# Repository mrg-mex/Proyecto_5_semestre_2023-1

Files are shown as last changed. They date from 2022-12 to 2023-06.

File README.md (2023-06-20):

# Proyecto_5_semestre_2023-1
# Diseño y simulación de un robot manipulador móvil

# Robótica serial adaptable

# Participantes
- Erik Peña Medina (responsable)
- Garcia Oñate Miguel Angel
- Mendoza Reyes Carlos Mauricio
- Lazcano Romero Eduardo Alejandro
- Torres Guerrero Adair

# Objetivo
Diseñar e generar los elmentos para la simulación y construcción de un manipulador móvil, compuesto por una base móvil omnidireccional y un robot serial Dofbot.

# Metas
- Determinar los parámetros relacionados con las dimensines de los elementos que componene al robot.
- Establecer una distribución de los elementos que conforman la base móvil de tal manera que sus dimensiones sean considetnes las dimensiones del robot ROSMASTER X3 PLUS ROS Robot.
- Realizar el diseño a detalle del robot en CAD y generar los elementos de la simulación virtual del robot.
- Diseño y construcción de los circuitos de la PCB necesarios para la implimientación del robot. 

---
# Productos
- Diseño a detalle del la plataforma móvil.
- Desarrollo de los elementos de una simulación Virtual del robot en formato URDF.
- Diseño y realización de los circuitos de control y de potencia del robot en formato PCB.
- Desarrollo de los elementos para la construcción del manipulador móvil de manera física.

---
## Primer día, mié 30/11/22
- Instalacion SW 2020
- Inicio de planeación → probablemente iniciaremos con esquemáticos del robot
ROSMASTER X3 PLUS para comparar sus dimensiones y distribución con el actual
(Requerimos SW)
- Descargamos dofbot-cad-min.zip, el cad del robot. En este repo GITHUB
---
## Segundo dia, lun 05/12/22
- afecta la forma de la base? por que mantener el track?
- qué lleva el piso inferior? el comercial es mas chico, por qué lo queremos mas
grande?
- donde posicionar los soportes del motor?

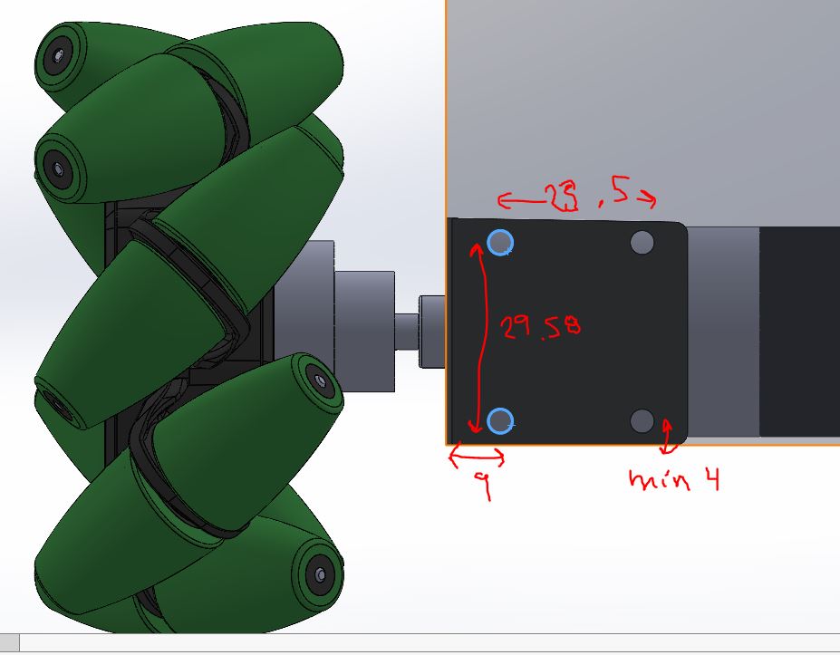
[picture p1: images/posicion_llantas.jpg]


---
## Lun 12/12/2022 fue puente
---
## Tercer dia, mie 14/12/22
- cads de partes faltantes
- distribucion de los elementos en los pisos
- tamaño de los pisos y alturas chance

Abajo se muestran las dimensiones preliminares del tamaño de los pisos

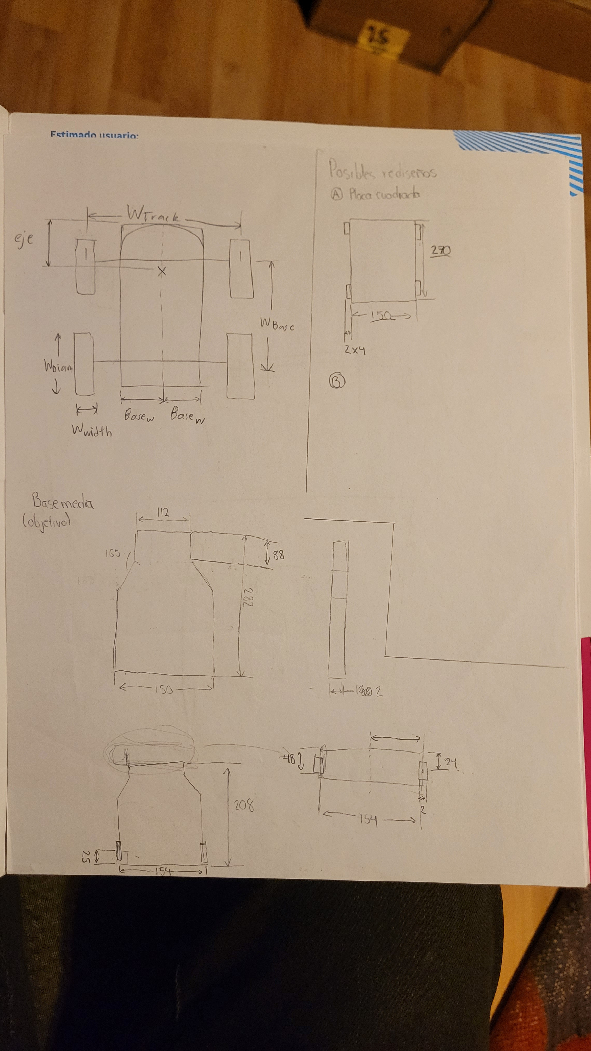
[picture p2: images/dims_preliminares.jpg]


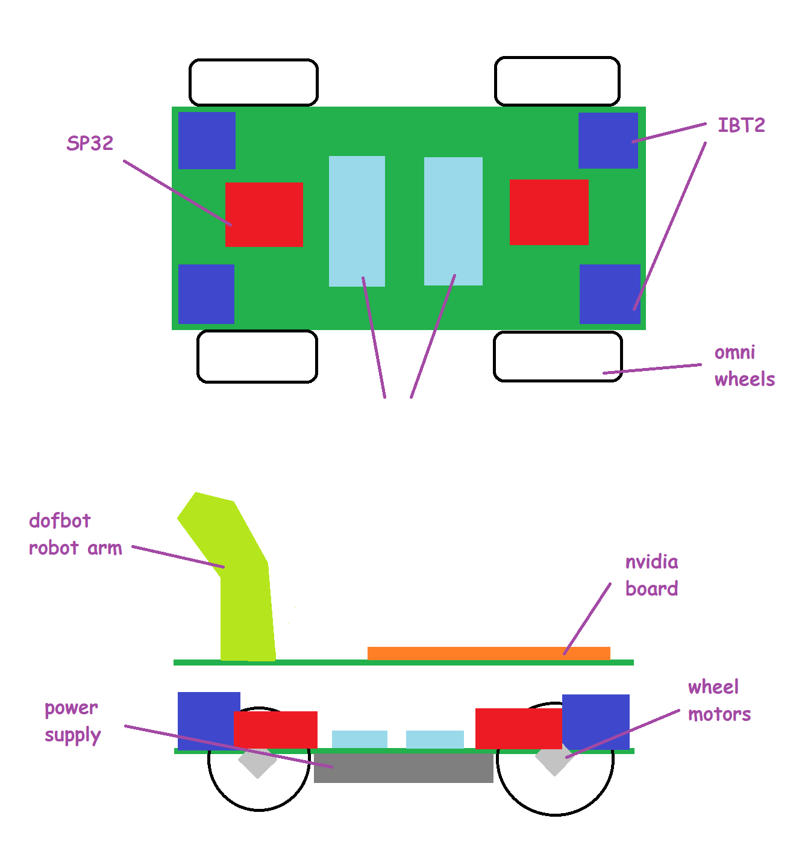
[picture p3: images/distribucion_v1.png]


---

## Cuarto día, mie 11/01/23
- La placa inferior del diseño comercial tiene unas dimensiones de 280 mm x 150 mm. Sin embargo, estas medidas no pueden ser tomadas debido al tamaño de la batería que chocaría con los motores.
Se propuso una placa inferior de 200 mm x 320 mm basándonos en las medidas del primer prototipo fabricado con MDF por el profesor Erik Peña Medina. La placa seguía siendo pequeña para posicionar la batería en la parte inferior.
Al final se propuso una placa de 320 mm x 170 mm la cual permitió tener el suficiente espacio para distribuir los componentes y realizar los respectivos agujeros para el cableado.

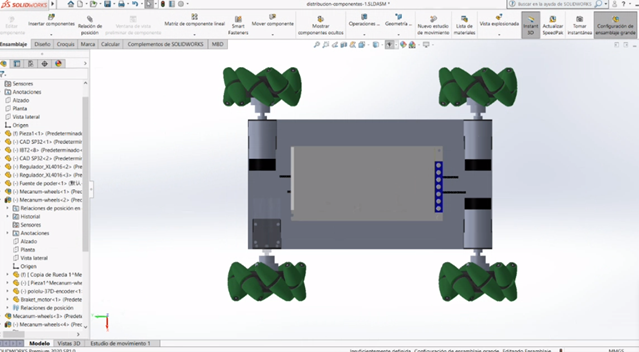
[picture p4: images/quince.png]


### Distancia entre motores
Para la propuesta de la distancia entre motores el equipo se basó en la distancia del robot comercial la cual es de 44 mm. Esta distancia entre motores es importante ya que le dará estabilidad al robot móvil.

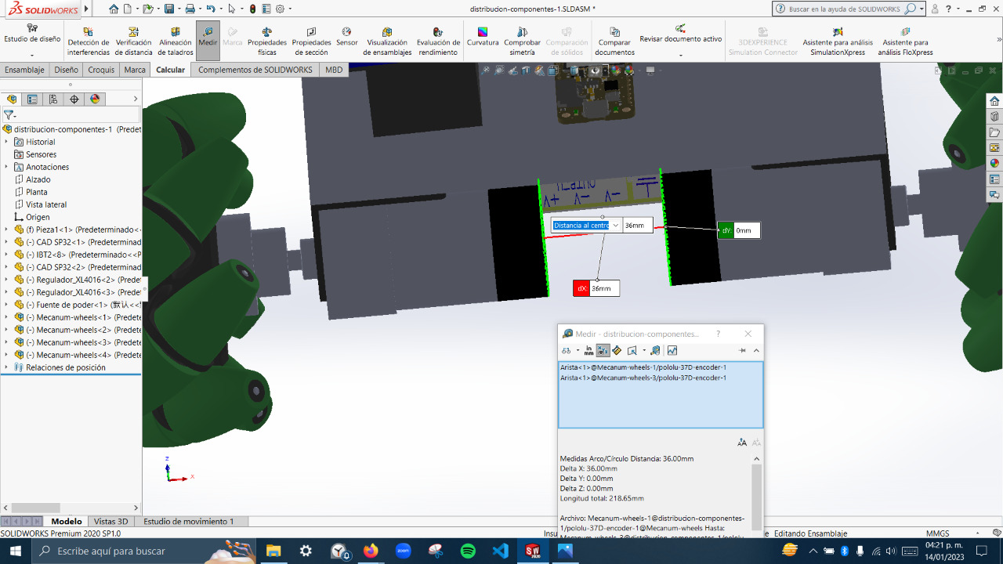
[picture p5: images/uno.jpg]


### Orientación de IBT2
Por cada motor existirá un IBT2 y la para proponer la orientación más óptima de estos componentes se consideró las conexiones entre componentes.

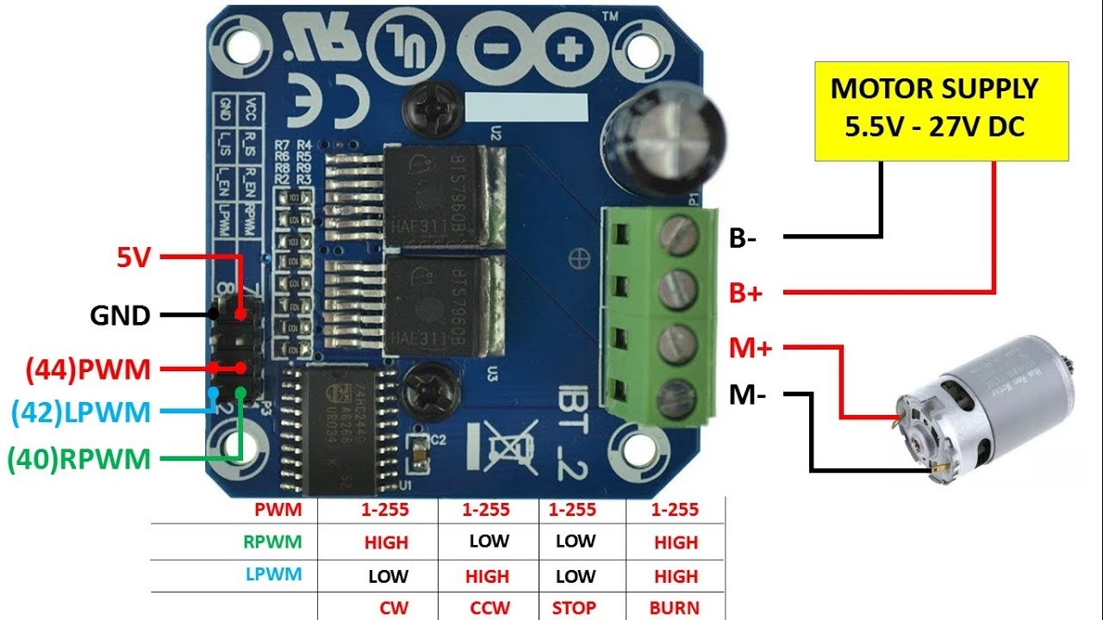
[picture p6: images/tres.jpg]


A continuación, se muestra el diagrama de conexiones entre componentes:

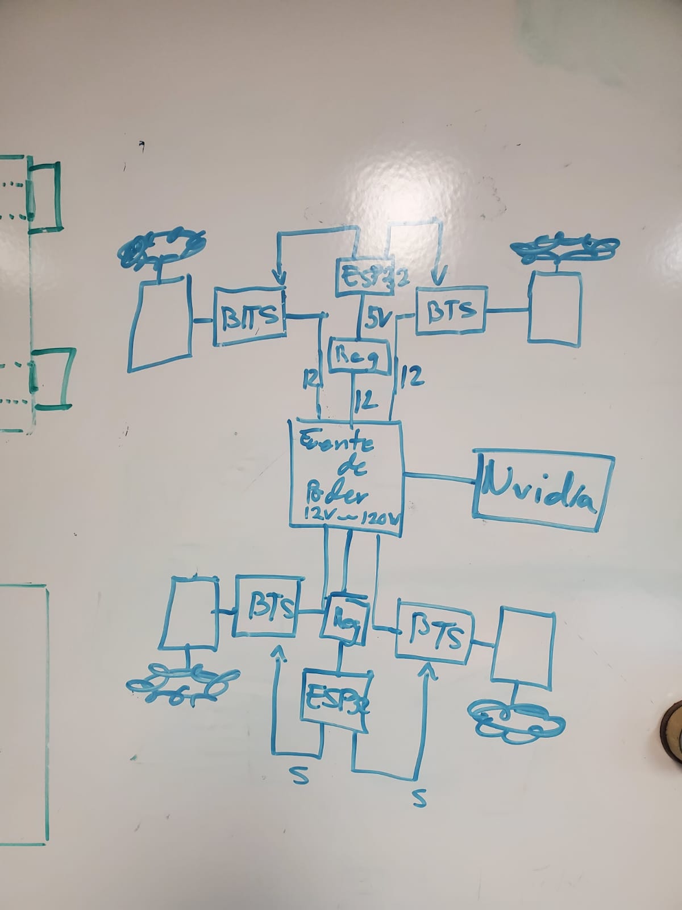
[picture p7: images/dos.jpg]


### Orientación final propuesta:

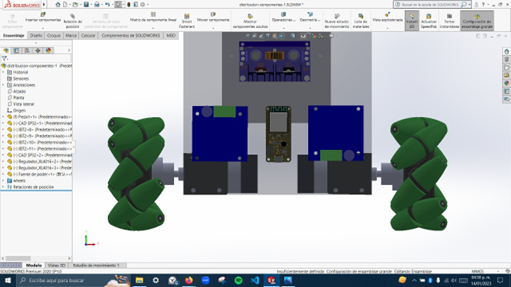
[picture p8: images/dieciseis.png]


### Propuesta montaje de PCB
Al no conocer las dimensiones de la PCB se propuso crear un piso intermedio en voladizo. Se muestra la propuesta en la siguiente imagen:
 
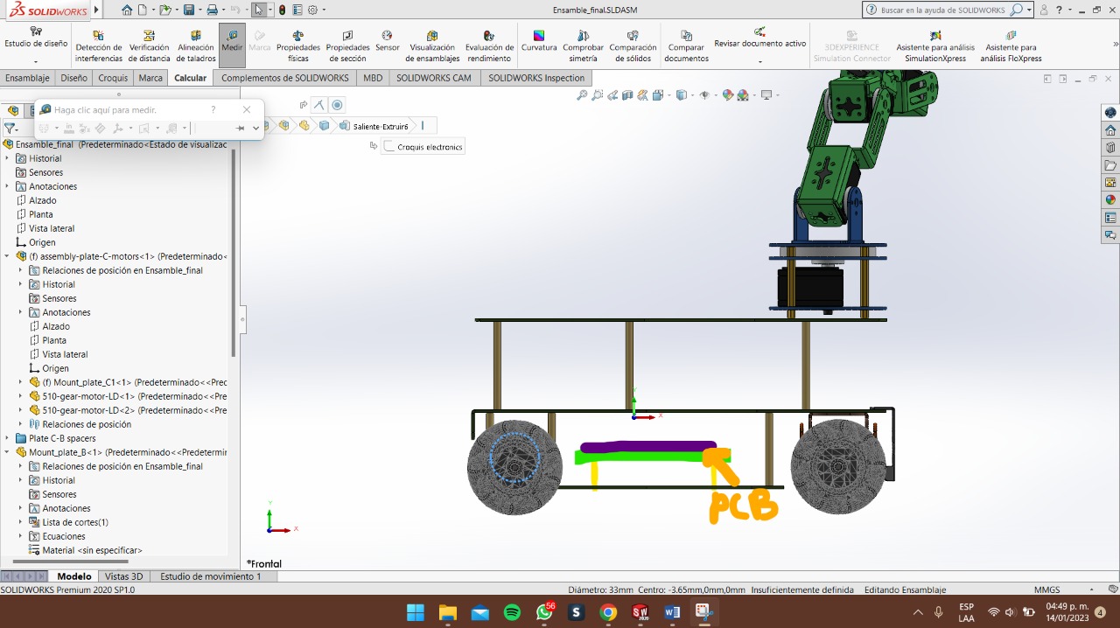
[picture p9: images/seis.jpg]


Para simular la PCB y realizar el montaje de los componentes se insertaron dos protoboards.

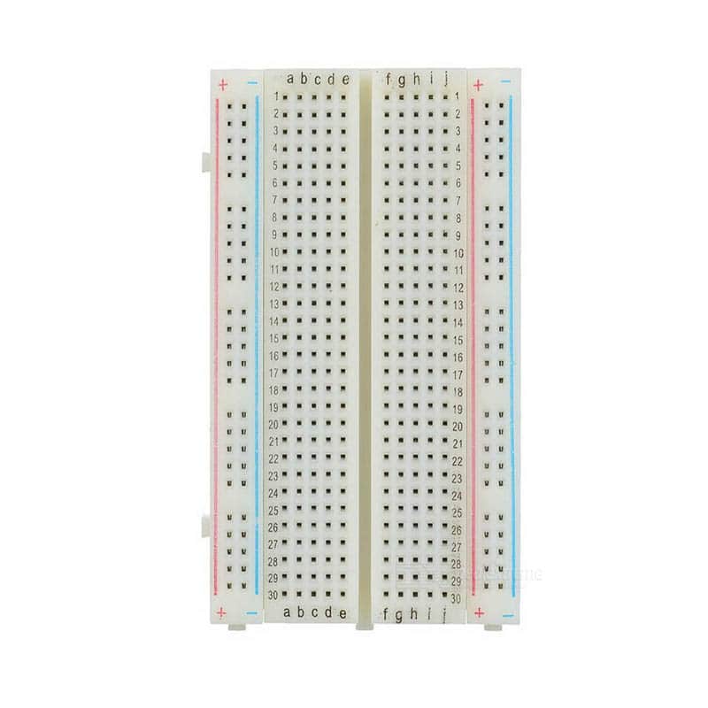
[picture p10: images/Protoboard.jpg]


### Ensamble de componentes principales
Nos encontramos con el problema de no poder ensamblar los componentes a la placa inferior debido a todo el espacio que ocupa la batería. Para solucionar esto, se propuso un piso superior en donde se montaron cada uno de los IBT2. 

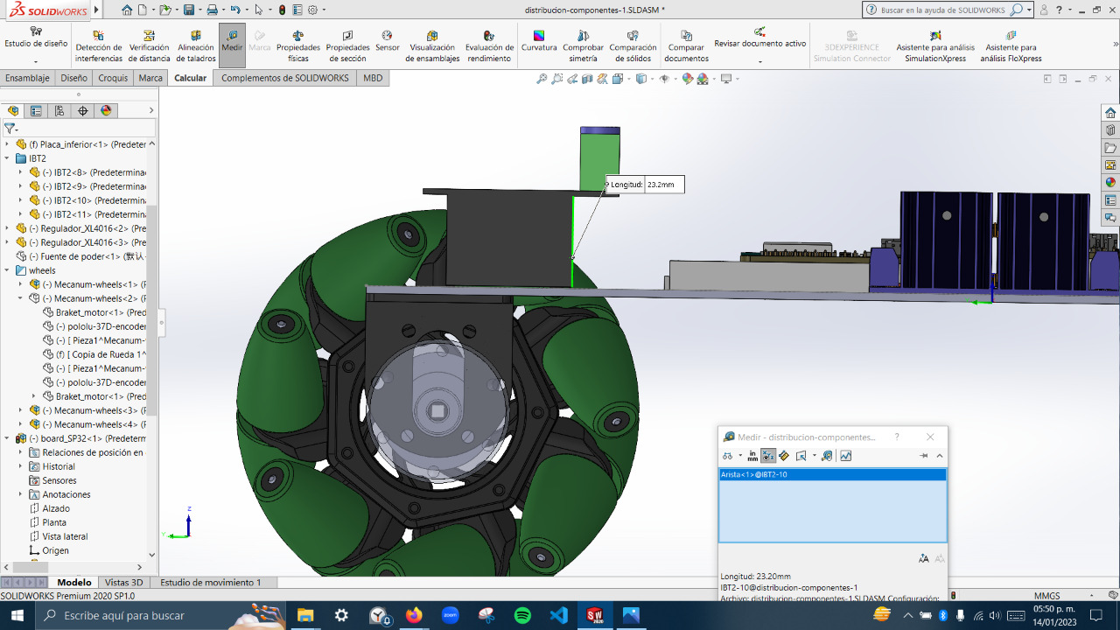
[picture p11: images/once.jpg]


Los IBT2 se montaron en voladizo esto ayudará a mejorar el paso del aire a través de los disipadores.

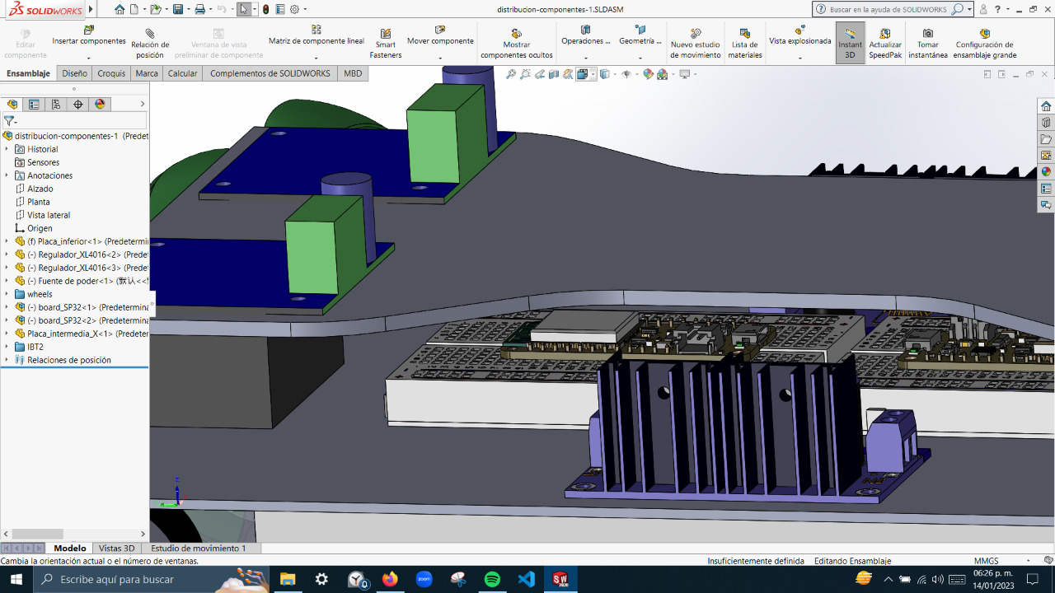
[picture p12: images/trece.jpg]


### Diseño del segundo Piso del Robot, para ensamblaje del brazo.
En este punto, se contempló que nuestro diseño (una vez optimizado el espacio) debería contener unas columnas que nos permitieran dejar un piso libre
para ensamblar el brazo del modelo comercial.

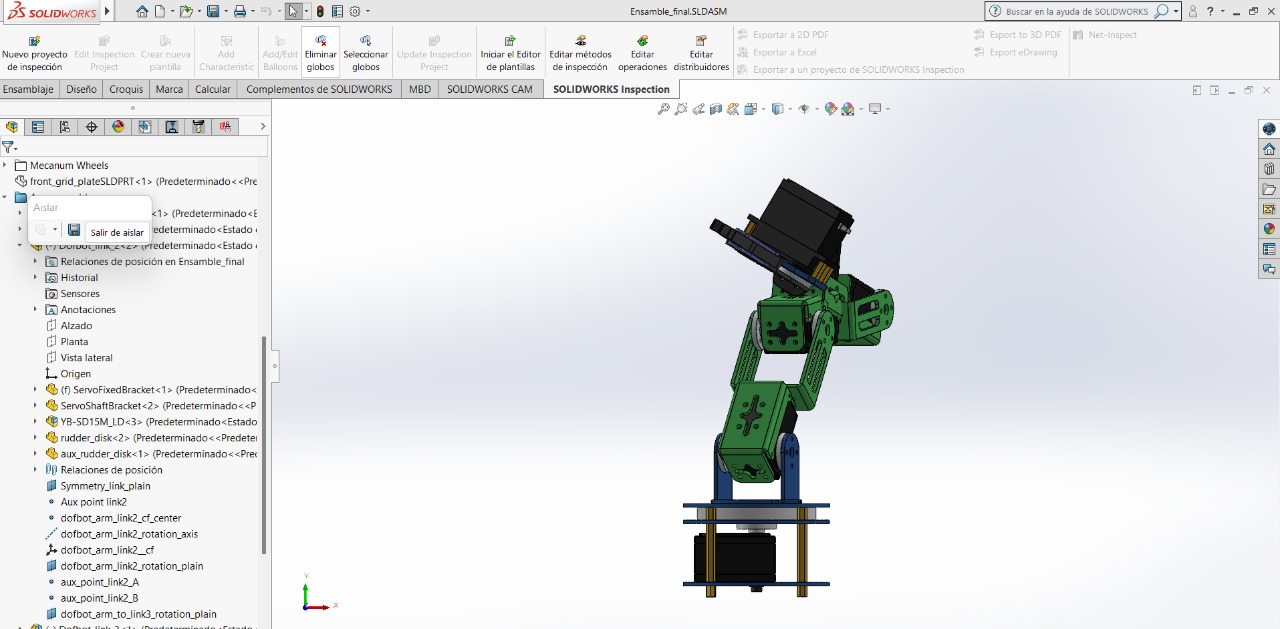
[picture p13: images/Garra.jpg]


### Implementación del segundo piso del robot
Una vez planificado el espacio donde se implementarán las columnas, se procedió a realizar el modelado final:
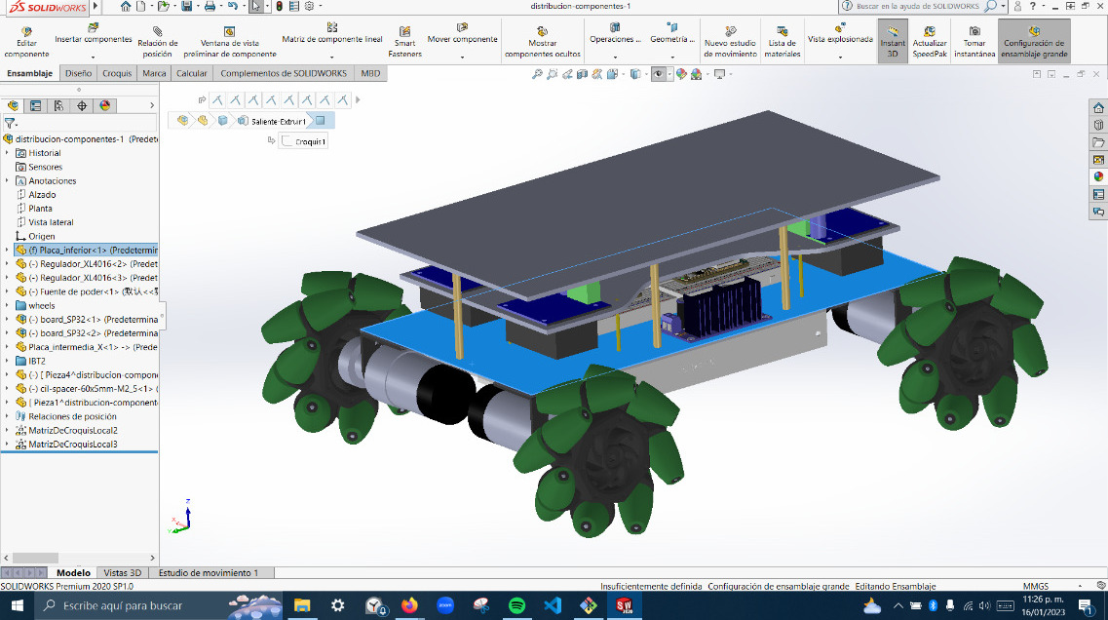
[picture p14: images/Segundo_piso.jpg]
Imagen de una segunda plataforma sobre el diseño previamente mostrado


### Ensamble del brazo robotico:
Para esta parte, se buscó establecer la pieza cercano al centro de masa, de tal modo que no afectara la localización de la Nvidia y pudiera cubrir los requerimientos 
planteados por el profesor.

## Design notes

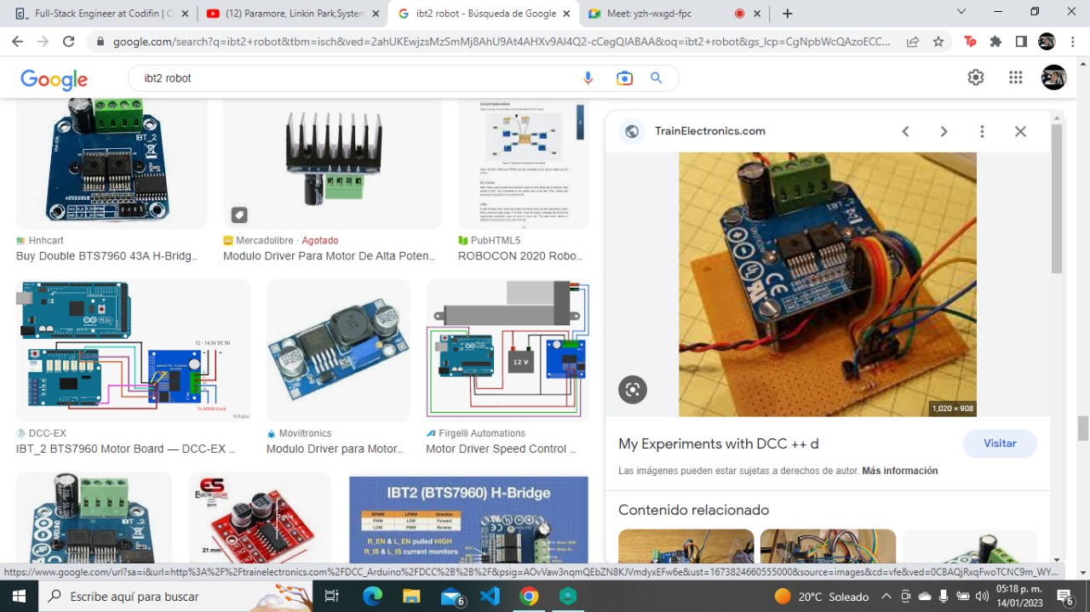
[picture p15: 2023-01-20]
images/siete.jpg

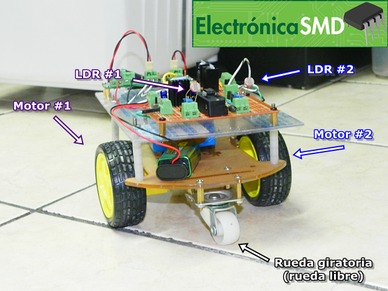
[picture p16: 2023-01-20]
images/cinco.jpg

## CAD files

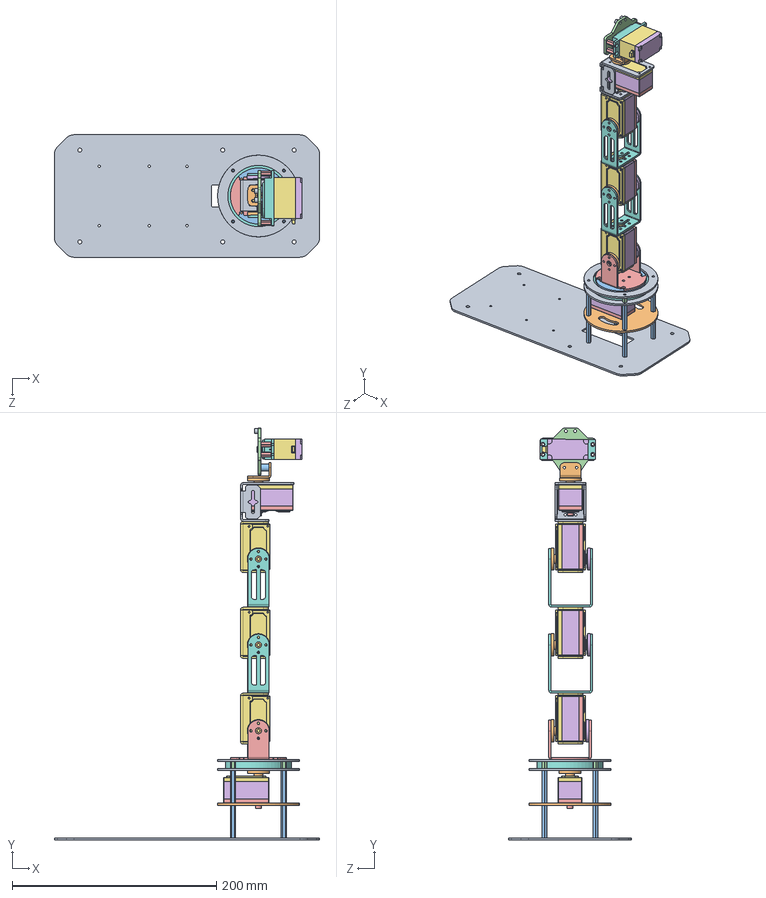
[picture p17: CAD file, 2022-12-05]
Arm_urdf.SLDASM
260.0 x 403.5 x 120.0 mm
Placa_Base
base_ring_2
M2,5_hex_standoff_32mm x 8
Hex_nut_7mm_ig_ig_3.6mm x 4
YB-SD15M-Bottom-Cover-LD x 5
YB-SD15M-Middle-Cover-LD x 5
YB-SD15M-Top-Cover-LD x 5
Sealed-Ball-Bearing-50x65x7mm
Base_ring x 2
rudder_disk x 5
Base_spin_disk x 2
cil_7mm_spacer x 4
link_shaft_bracket
aux_rudder_disk x 3
ServoFixedBracket x 3
ServoShaftBracket x 2
ServoFixedBracket_Type_C
shaft-rudder-coupler
Cil-spacer-7x10-inn-3mm x 2
Mount-plate
Hex_nut_10mm_ig_ig_2,5mm x 4
YB-SSERVO-6KG-Bottom
YB-SSERVO-6KG-Middle
YB-SSERVO-6KG-Top
Cil-spacer-3x5-inn-3mm x 2

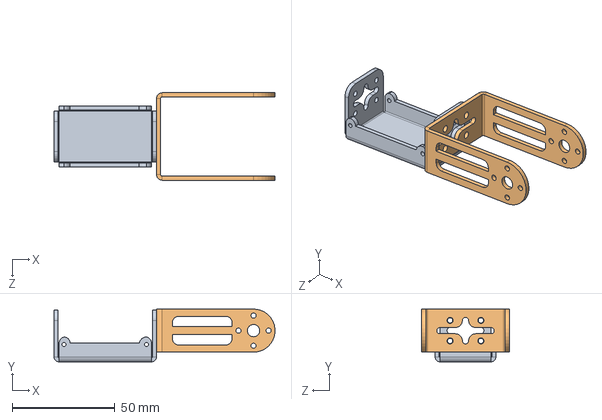
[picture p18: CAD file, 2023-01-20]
Ensable_final_robotica/Ensamble_robot_comercial/Link_type_A.SLDASM
107.7 x 25.7 x 42.7 mm
ServoFixedBracket
ServoShaftBracket

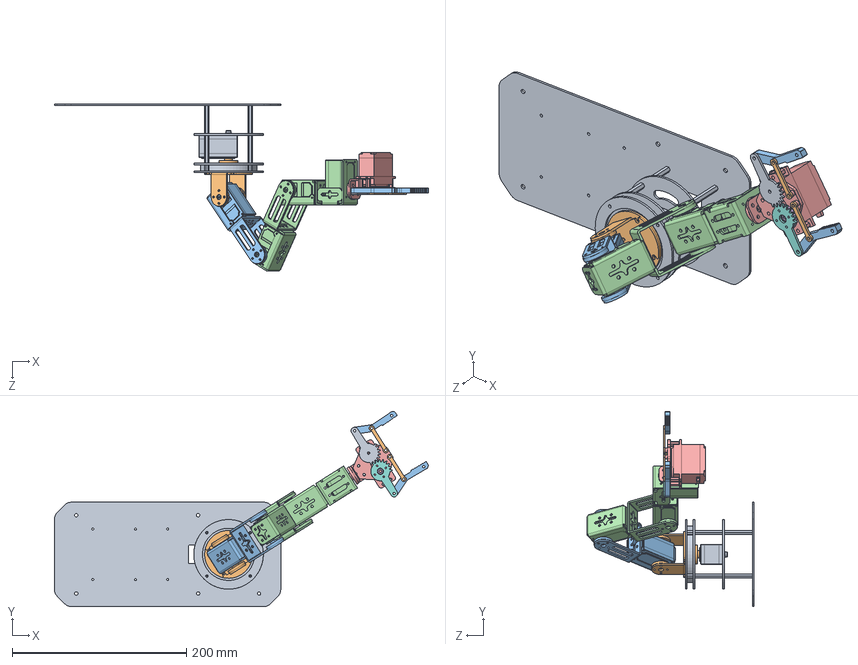
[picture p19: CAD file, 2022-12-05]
Simplificado/Dofbot_esamble_simplify.SLDASM
429.7 x 224.2 x 192.1 mm
Dofbot_base_link_simplificado
Dofbot_link_1_sim
Dofbot_link_2_sim
Dofbot_link4_simplificado
Dofbot_link_5_simplificado
rudder_disk
finger-spacer
finger-rgt-gear
finger-lft-gear
finger-bar x 2
rfinger_tip x 2
Dofbot_link_3_sim

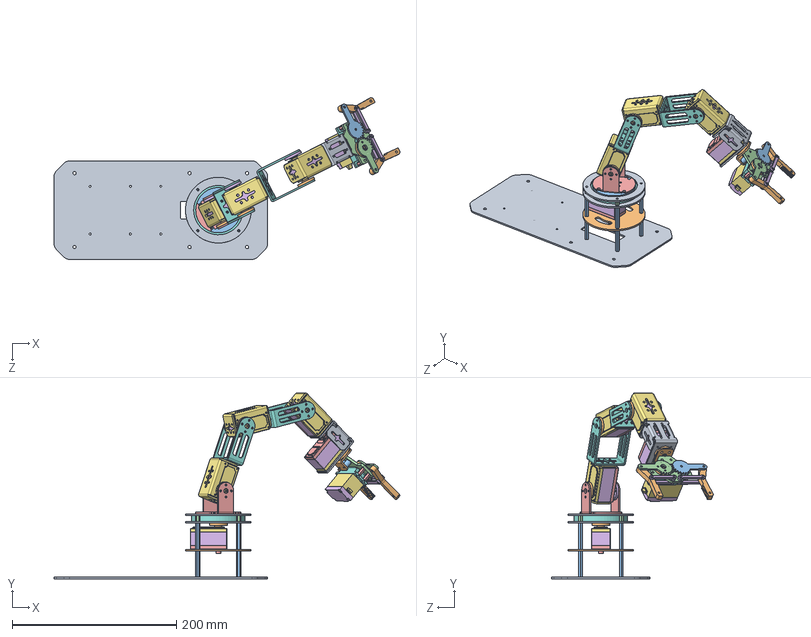
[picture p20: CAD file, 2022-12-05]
Arm_Simscape.SLDASM
421.1 x 226.0 x 197.0 mm
Placa_Base
base_ring_2
M2,5_hex_standoff_32mm x 8
Hex_nut_7mm_ig_ig_3.6mm x 4
YB-SD15M-Bottom-Cover-LD x 5
YB-SD15M-Middle-Cover-LD x 5
YB-SD15M-Top-Cover-LD x 5
Sealed-Ball-Bearing-50x65x7mm
Base_ring x 2
rudder_disk x 6
Base_spin_disk x 2
cil_7mm_spacer x 4
link_shaft_bracket
aux_rudder_disk x 3
ServoFixedBracket x 3
ServoShaftBracket x 2
ServoFixedBracket_Type_C
shaft-rudder-coupler
Cil-spacer-7x10-inn-3mm x 2
Mount-plate
Hex_nut_10mm_ig_ig_2,5mm x 4
YB-SSERVO-6KG-Bottom
YB-SSERVO-6KG-Middle
YB-SSERVO-6KG-Top
Cil-spacer-3x5-inn-3mm x 4
rfinger_tip x 2
finger-lft-gear
finger-rgt-gear
finger-spacer
finger-bar x 4

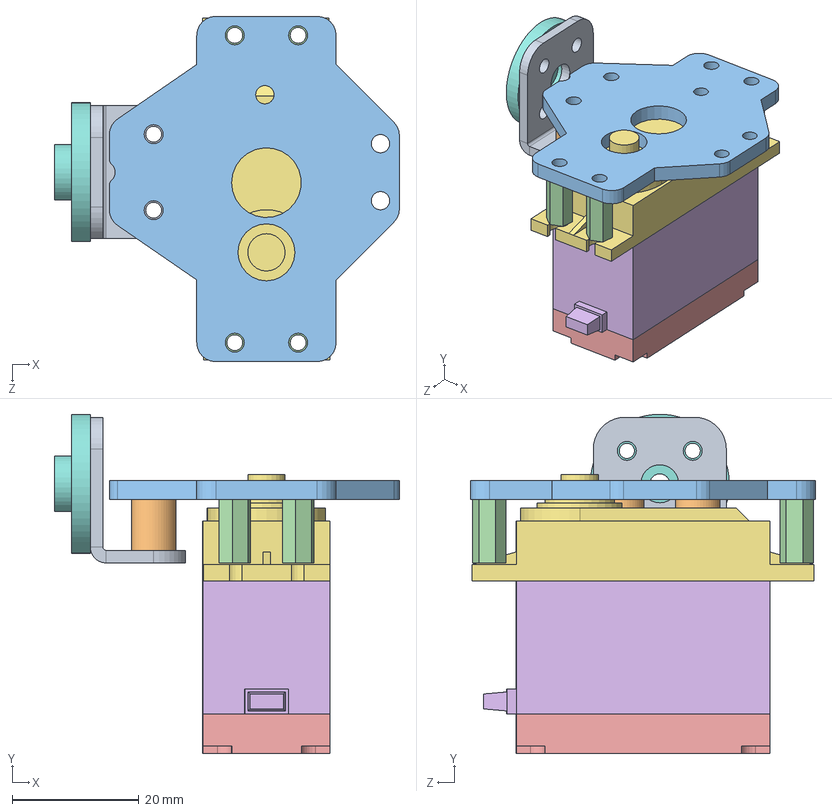
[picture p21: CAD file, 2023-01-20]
Ensable_final_robotica/Ensamble_robot_comercial/Dofbot_link_5.SLDASM
54.5 x 53.6 x 54.5 mm
shaft-rudder-coupler
Cil-spacer-7x10-inn-3mm x 2
Mount-plate
Hex_nut_10mm_ig_ig_2,5mm x 4
YB-SSERVO-6KG-Bottom
YB-SSERVO-6KG-Middle
YB-SSERVO-6KG-Top
rudder_disk

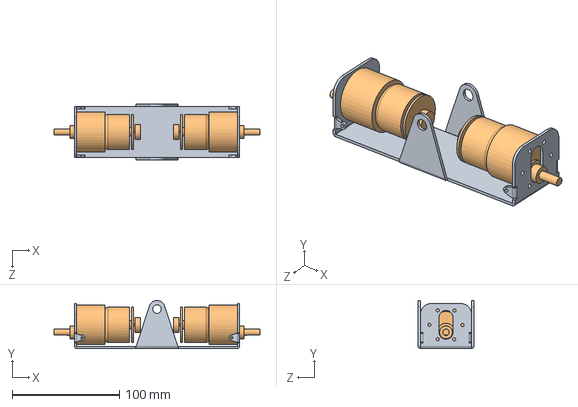
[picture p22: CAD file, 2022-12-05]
Ensable_final_robotica/Ensamble_robot_comercial/Movil/assembly-plate-Cb-motors.SLDASM
192.2 x 44.8 x 52.0 mm
Mount_plate_C2_bottom
510-gear-motor-LD x 2

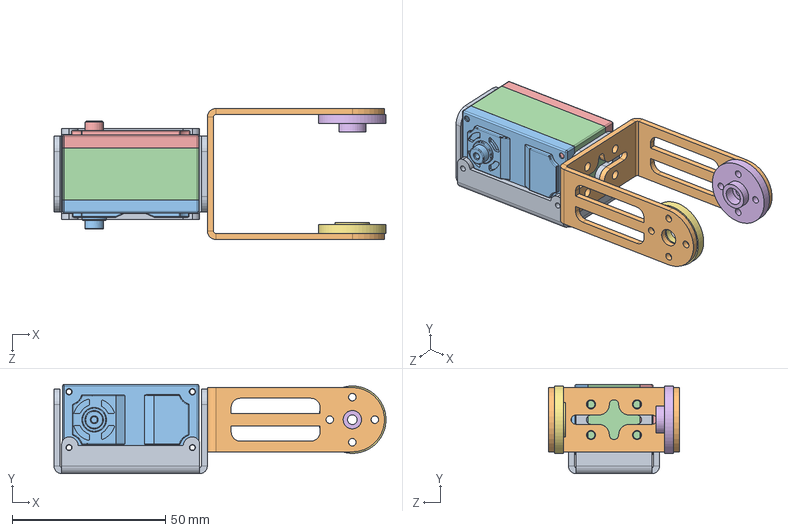
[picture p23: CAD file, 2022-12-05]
Simplificado/Dofbot_link_2_simplificado.SLDASM
108.2 x 29.1 x 42.7 mm
ServoFixedBracket
ServoShaftBracket
YB-SD15M-Bottom-Cover-LD
YB-SD15M-Middle-Cover-LD
YB-SD15M-Top-Cover-LD
rudder_disk
aux_rudder_disk

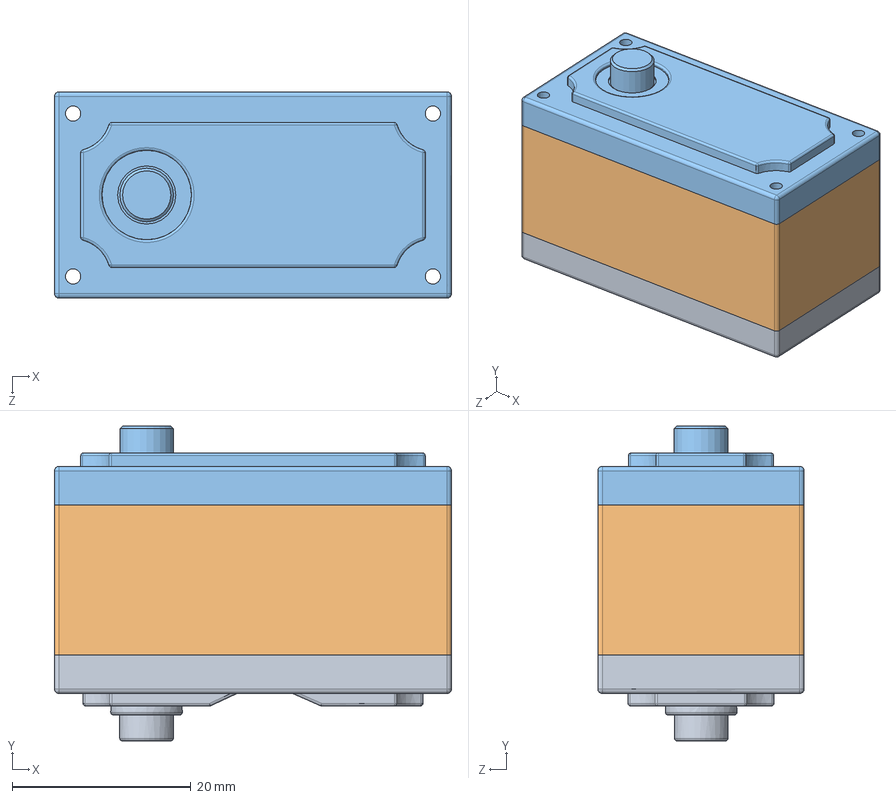
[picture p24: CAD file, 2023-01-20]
Ensable_final_robotica/Ensamble_robot_comercial/YB-SD15M-LD/YB-SD15M_LD.SLDASM
44.4 x 35.2 x 23.1 mm
YB-SD15M-Bottom-Cover-LD
YB-SD15M-Middle-Cover-LD
YB-SD15M-Top-Cover-LD

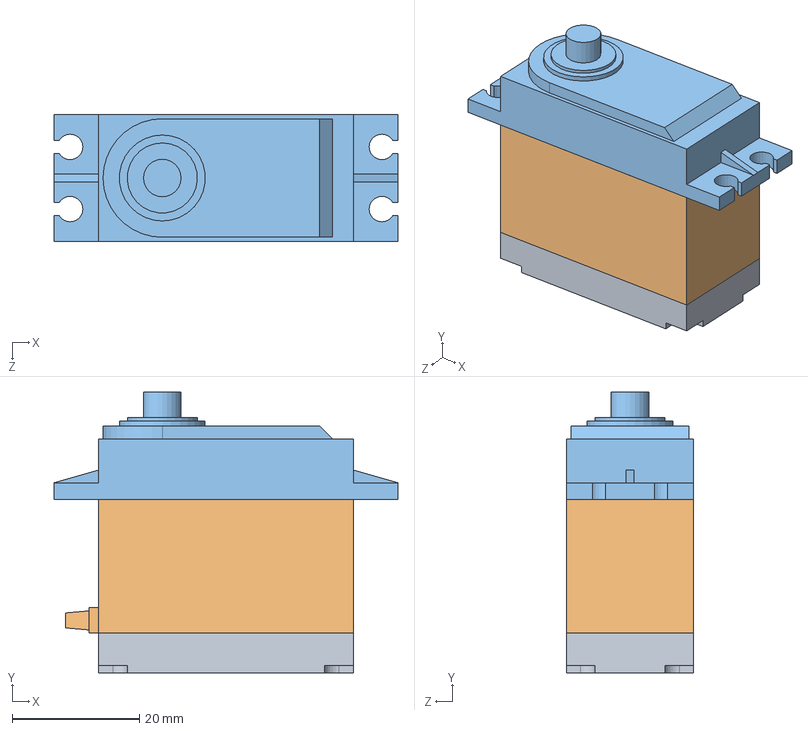
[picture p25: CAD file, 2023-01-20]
Ensable_final_robotica/Ensamble_robot_comercial/YB-SERVO-6KG-LD/YB-SERVO-6KG-LD.SLDASM
54.0 x 44.1 x 20.0 mm
YB-SSERVO-6KG-Bottom
YB-SSERVO-6KG-Middle
YB-SSERVO-6KG-Top

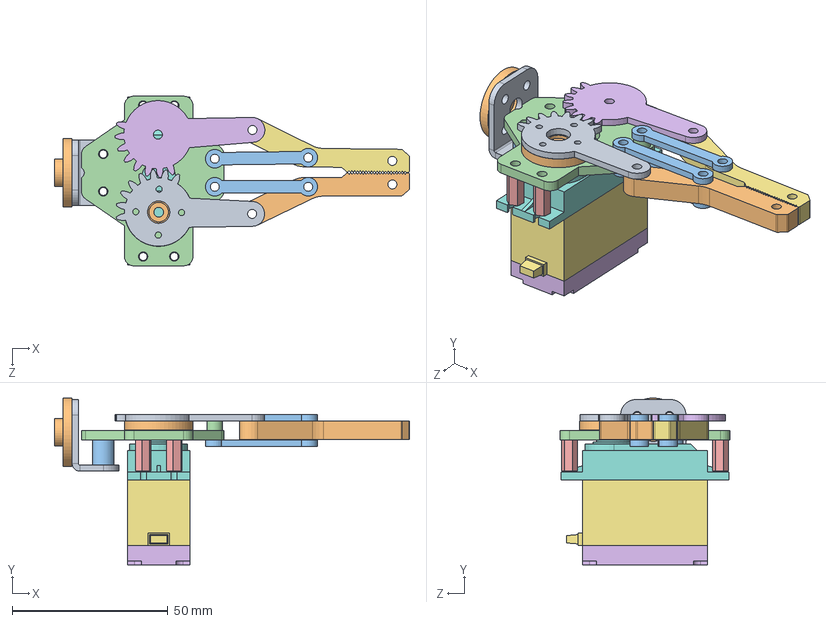
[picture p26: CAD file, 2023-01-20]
Ensable_final_robotica/Ensamble_robot_comercial/Gripper_v3_urdf.SLDASM
114.0 x 53.6 x 54.5 mm
shaft-rudder-coupler
rudder_disk x 2
Cil-spacer-7x10-inn-3mm x 2
Mount-plate
Hex_nut_10mm_ig_ig_2,5mm x 4
YB-SSERVO-6KG-Bottom
YB-SSERVO-6KG-Middle
YB-SSERVO-6KG-Top
finger-rgt-gear
rfinger_tip
finger-bar x 4
Cil-spacer-3x5-inn-3mm x 2
finger-spacer
finger-lft-gear
lfinger_tip

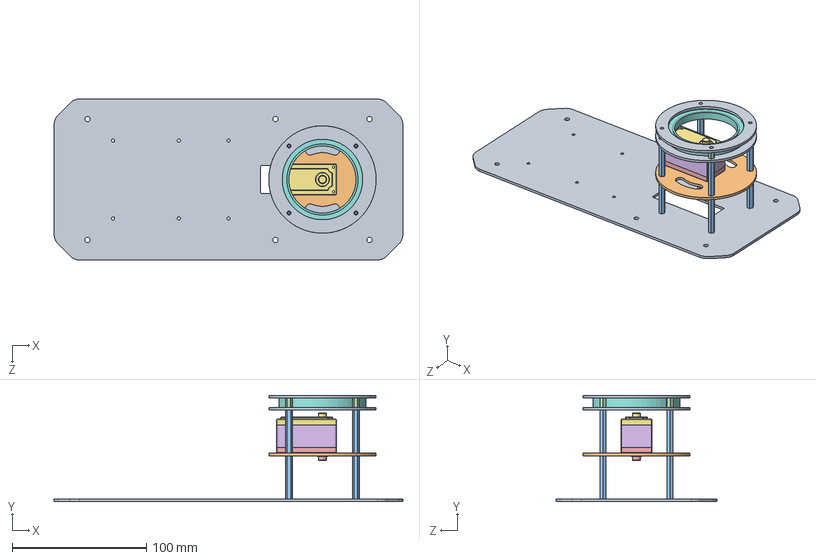
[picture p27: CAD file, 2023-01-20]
Ensable_final_robotica/Ensamble_robot_comercial/Dofbot_base_link.SLDASM
260.0 x 79.0 x 120.0 mm
Placa_Base
base_ring_2
M2,5_hex_standoff_32mm x 8
Hex_nut_7mm_ig_ig_3.6mm x 4
YB-SD15M-Bottom-Cover-LD
YB-SD15M-Middle-Cover-LD
YB-SD15M-Top-Cover-LD
Sealed-Ball-Bearing-50x65x7mm
Base_ring x 2

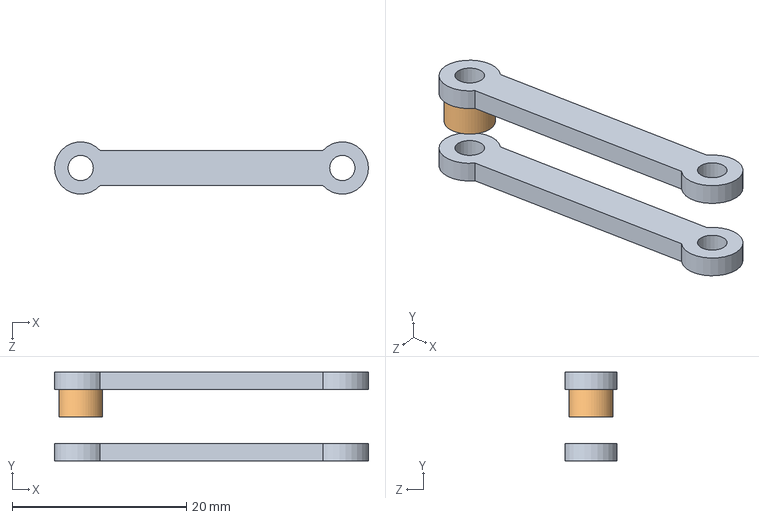
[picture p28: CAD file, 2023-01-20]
Ensable_final_robotica/Ensamble_robot_comercial/Gripper/twin_bars_assembling.SLDASM
36.0 x 10.1 x 5.96 mm
finger-bar x 2
Cil-spacer-3x5-inn-3mm

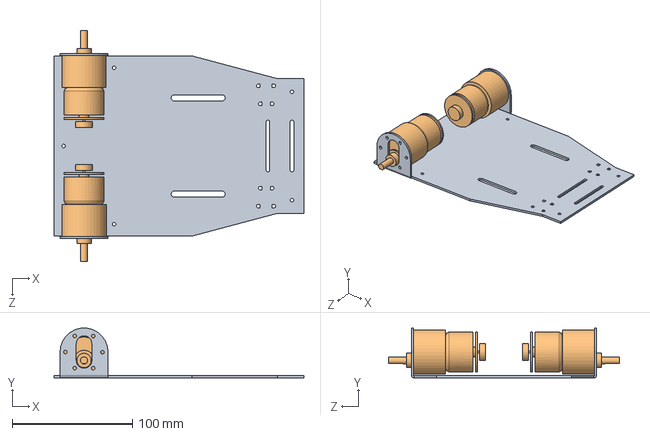
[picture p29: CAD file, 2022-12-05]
Ensable_final_robotica/Ensamble_robot_comercial/Movil/assembly-plate-C-motors.SLDASM
208.0 x 41.4 x 192.2 mm
Mount_plate_C1
510-gear-motor-LD x 2

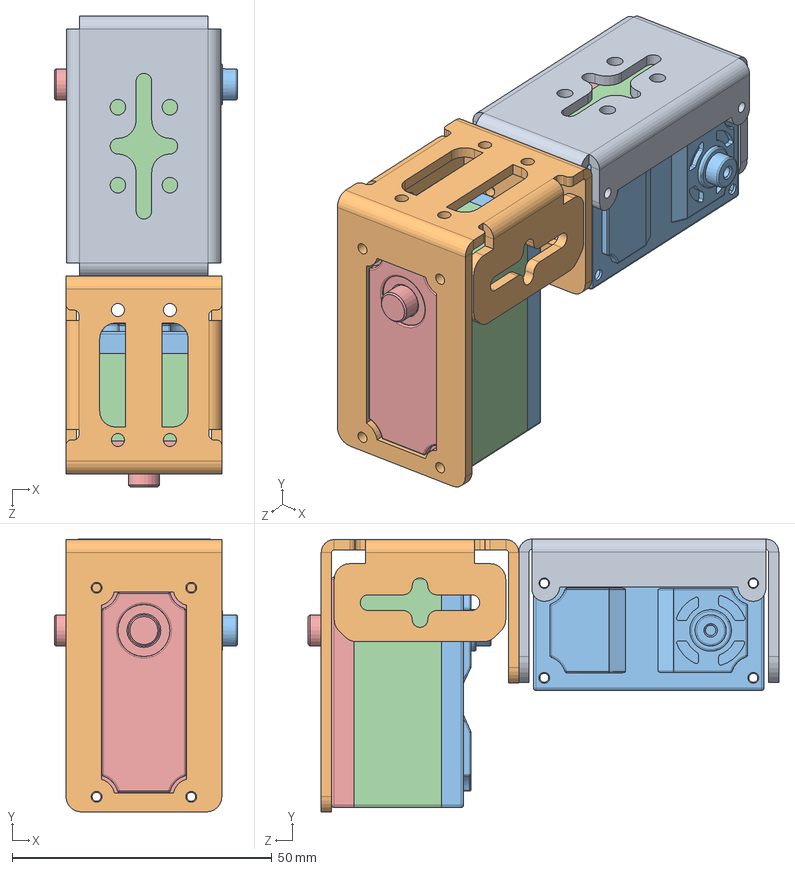
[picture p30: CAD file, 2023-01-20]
Ensable_final_robotica/Ensamble_robot_comercial/Dofbot_link_4.SLDASM
35.2 x 52.5 x 90.5 mm
ServoFixedBracket
ServoFixedBracket_Type_C
YB-SD15M-Bottom-Cover-LD x 2
YB-SD15M-Middle-Cover-LD x 2
YB-SD15M-Top-Cover-LD x 2

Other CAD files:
Ensable_final_robotica/Ensamble_robot_comercial/Dofbot_link_2.SLDASM
Ensable_final_robotica/Ensamble_robot_comercial/Dofbot_link_3.SLDASM
Ensable_final_robotica/Ensamble_robot_comercial/Ensamble_final.SLDASM
Ensable_final_robotica/Ensamble_robot_comercial/Dofbot_Arm.SLDASM
Base_ring.SLDPRT
Ensable_final_robotica/Braket_motor.SLDPRT
Ensable_final_robotica/Ensamble_robot_comercial/510-Gear-Motor/510-gear-motor-LD.SLDPRT
Ensable_final_robotica/Ensamble_robot_comercial/510-Gear-Motor/6mm_Hex_coupling_.SLDPRT
Ensable_final_robotica/Ensamble_robot_comercial/6810rs1_65od_50id_7w.SLDPRT
Ensable_final_robotica/Ensamble_robot_comercial/Arm_urdf.SLDASM
Ensable_final_robotica/Ensamble_robot_comercial/Base_ring.SLDPRT
Ensable_final_robotica/Ensamble_robot_comercial/Base_spin_disk.SLDPRT
Ensable_final_robotica/Ensamble_robot_comercial/Camera.SLDPRT
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

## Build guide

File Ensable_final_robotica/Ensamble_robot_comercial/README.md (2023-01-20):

# dofbot-cad
Modelo CAD realizado en Solidworks 2020 del Robot Dofbot

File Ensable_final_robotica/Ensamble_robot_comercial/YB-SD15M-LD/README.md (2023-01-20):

# YB-SD15M Servomotor CAD Files (Low detail)

Yahboom **YB-SD15M** Servomotor Low-Detail CAD files. Solidworks 2020.

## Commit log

2022-12-04 Primer Commit
    Borrador de proyecto
2022-12-05 Commit piezas del manipulador móvil
    Archivos de referencia para los parámetros del robot manipulador.
    [510-gear-motor-LD.SLDPRT, 6810rs1_65od_50id_7w.SLDPRT, 6mm_Hex_coupling_.SLDPRT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]
